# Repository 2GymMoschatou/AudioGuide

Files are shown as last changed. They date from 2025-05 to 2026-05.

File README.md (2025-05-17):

# AudioGuide
Αυτόνομο όχημα ηχητικής ξενάγησης

Πολλές φορές, για την ξενάγηση σε διάφορους χώρους ή μουσεία, μπορεί να είναι χρήσιμη η ηχητική παρουσίαση των εκθεμάτων για άτομα με προβλήματα όρασης. Με τη χρήση ενός ρομπότ-ξεναγού, μπορούμε να βοηθήσουμε τα άτομα αυτά να ξεναγηθούν στο μουσείο.
Το ρομπότ ακολουθεί μια προκαθορισμένη διαδρομή, σχεδιασμένη στο δάπεδο του χώρου των εκθεμάτων και σταματά διαδοχικά μπροστά σε κάθε έκθεμα. Σταματώντας, περιγράφει το έκθεμα και περιμένει την κατάλληλη εντολή για να συνεχίσει στο επόμενο, όπου η λειτουργία επαναλαμβάνεται. Όταν τελειώσει η ξενάγηση στα εκθέματα του χώρου, το ρομπότ επανέρχεται στην αφετηρία της διαδρομής, για να περιμένει την έναρξη ενός νέου κύκλου ξενάγησης.

Υλικά και κόστος του αυτόνομου οχήματος ηχητικής ξενάγησης:

|  Υλικά  |  Κόστος  |
|  ---  |  ---  |
|  Arduino Uno R3 (συμβατό)  |  9,90 €  |
|  Πλατφόρμα κίνησης με 4 κινητήρες  |  16,90 €  |
|  Οδηγός κινητήρων DC L298N  |  5,90 €  |
|  Αισθητήρας υπερύθρων (3 τεμ.)  |  4,80 €  |
|  Αισθητήρας υπερήχων  |  1,80 €  |
|  MP3 player Mini Module	  |  6,80 €  |
|  Κάρτα μνήμης microSDHC 32 Gb	|  6,80 €  |
|  Ηχείο 3W	|	2,40 €  |
|  Push Button|	0,50 €  |
|  Πλακέτα πρωτοτύπου για Arduino  |  1,80 €  |
|  Arduino long headers 6 pin  |  0,50 €  |
|  Arduino long headers 8 pin  |  0,50 €  |
|  Μπαταριοθήκη 6ΑΑ με διακόπτη  |  1,80 €  |
|  Μπαταρίες ΑΑ (6 τεμ.)	|  2,40 €  |
|  Σύνολο  |  62,80 €  |

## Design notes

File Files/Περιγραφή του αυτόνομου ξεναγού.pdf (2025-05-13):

# Αυτόνομο όχημα ηχητικής ξενάγησης

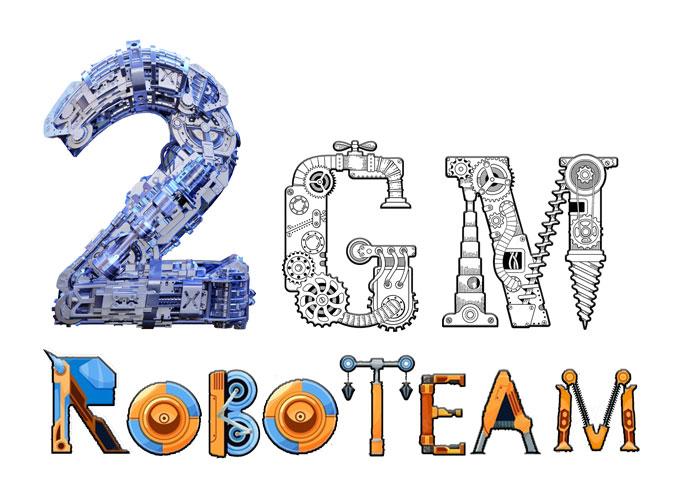
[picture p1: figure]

# 2ο Γυμνάσιο Μοσχάτου

# Σχολικό έτος 2024 - 25

## Περιγραφή του αυτόνομου οχήματος ηχητικής ξενάγησης

Το όχημα του αυτόνομου ξεναγού που σχεδιάσαμε έχει τη δυνατότητα να ακολουθεί μια μαύρη γραμμή στο δάπεδο του χώρου όπου θα κινηθεί. Για να σταματά στα σημεία που επιθυμούμε μπορεί να ανιχνεύσει τις κάθετες μαύρες γραμμές στη διαδρομή. Το όχημα ξεκινά από την είσοδο του χώρου, και ακολουθώντας τη γραμμή, σταματά διαδοχικά στις θέσεις που έχουμε ορίσει. Σε κάθε θέση αναπαράγει το αντίστοιχο αρχείο ήχου που έχουμε αποθηκεύσει στην κάρτα μνήμης. Για να ξεκινήσει από κάθε θέση και να προχωρήσει στην επόμενη, πρέπει να λάβει την κατάλληλη εντολή με το πάτημα ενός μπουτόν. Αν το όχημα ανιχνεύσει κάποιο εμπόδιο στη διαδρομή, τότε σταματά και περιμένει μέχρι να απομακρυνθεί το εμπόδιο.
Το όχημα θα μπορεί να χρησιμοποιηθεί βοηθητικά σε χώρους εκθέσεων, ιδιαίτερα για άτομα με προβλήματα όρασης.

## Σχεδίαση του αυτόνομου οχήματος ηχητικής ξενάγησης

Για την υλοποίηση του οχήματος χρησιμοποιήθηκε μια ρομποτική πλατφόρμα με τέσσερις κινητήρες DC, οι οποίοι ελέγχονται από μια πλακέτα με το ολοκληρωμένο ελέγχου L298N. Η ανίχνευση της διαδρομής του οχήματος πραγματοποιείται με τη βοήθεια τριών αισθητήρων υπερύθρων και η ανίχνευση τυχόν εμποδίων στη διαδρομή με ένα αισθητήρα υπερήχων. Η αναπαραγωγή των αρχείων ήχου γίνεται από μια μονάδα MP3 Player στην οποία συνδέεται ένα ηχείο 3 Watt. Η μονάδα διαθέτει μια υποδοχή για κάρτα μνήμης SD, όπου είναι αποθηκευμένα τα αρχεία ήχου. Οι εντολές για την κίνηση του οχήματος δίνονται από ένα μπουτόν. Το όχημα τροφοδοτείται από μια συστοιχία 6 μπαταριών ΑΑ, η οποίες περιέχονται σε μια μπαταριοθήκη με διακόπτη. Για τον έλεγχο του οχήματος χρησιμοποιείται η πλακέτα Arduino Uno.
Οι συνδέσεις των στοιχείων του οχήματος φαίνονται στο παρακάτω σχήμα:

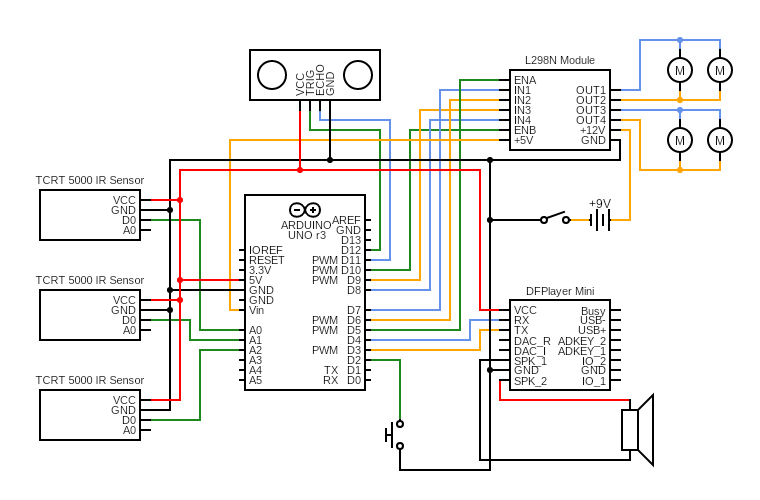
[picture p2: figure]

Το διάγραμμα των συνδέσεων δημιουργήθηκε με την δωρεάν online εφαρμογή δημιουργίας διαγραμμάτων ηλεκτρονικών κυκλωμάτων στη διεύθυνση www.circuit-diagram.org

## Συναρμολόγηση του αυτόνομου οχήματος ηχητικής ξενάγησης

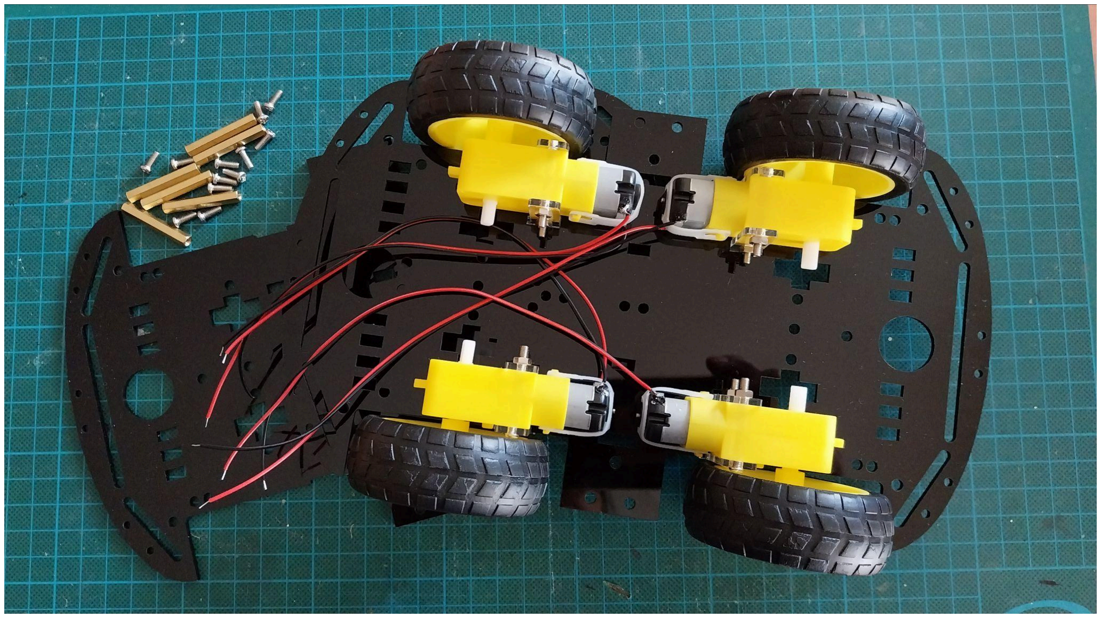
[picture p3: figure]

Η κατασκευή του οχήματος ξεκίνησε με την
τοποθέτηση των κινητήρων στο ένα τμήμα από το
σασί της πλατφόρμας.

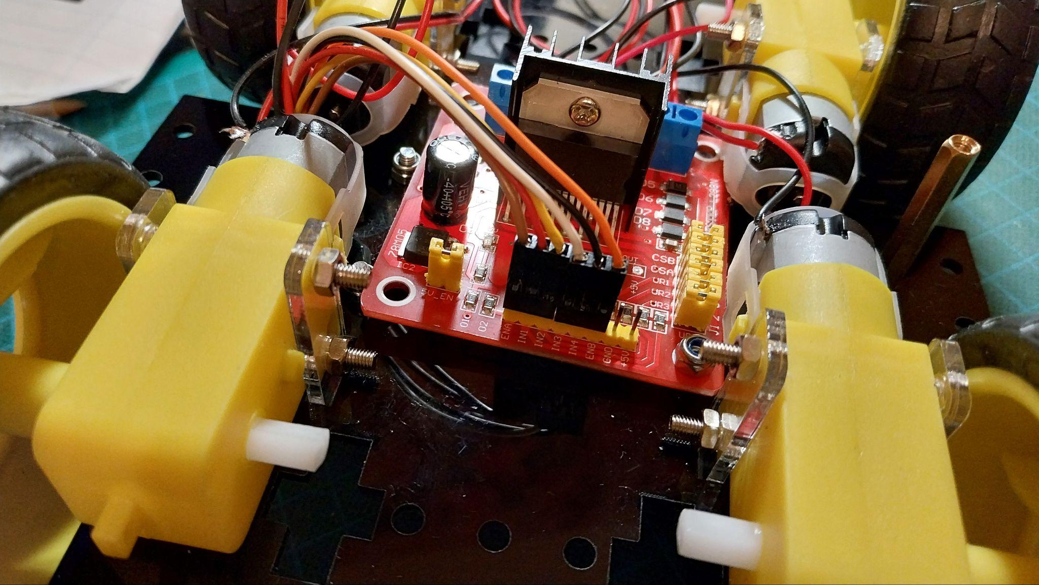
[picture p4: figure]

Ανάμεσα στους κινητήρες τοποθετήθηκε η πλακέτα με το ολοκληρωμένο L298N για την οδήγηση των κινητήρων. Στην πλακέτα συνδέθηκαν οι κινητήρες και η μπαταριοθήκη για την τροφοδοσία του οχήματος. Επίσης προετοιμάστηκαν οι καλωδιώσεις για τη σύνδεση με την πλακέτα του Arduino Uno.

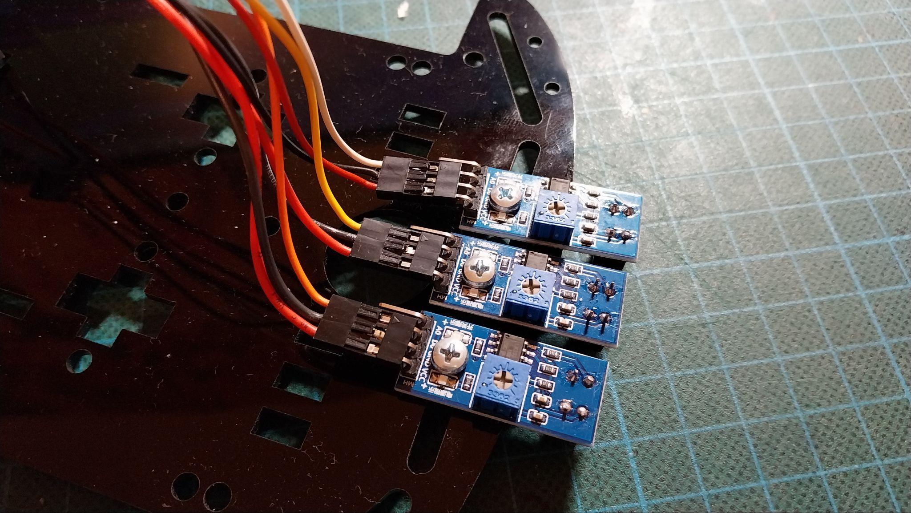
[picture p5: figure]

Στο δεύτερο τμήμα του σασί τοποθετήθηκαν οι αισθητήρες υπερύθρων με τις καλωδιώσεις τους.

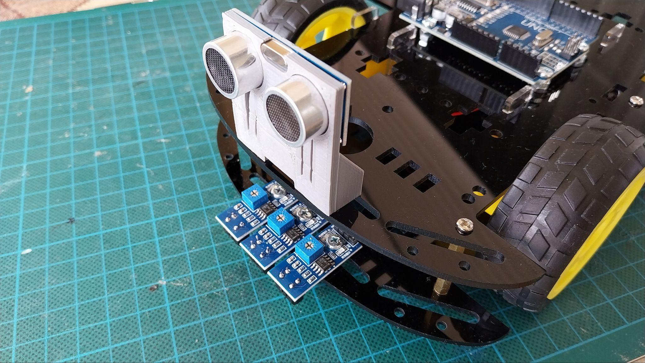
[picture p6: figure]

Τα δύο τμήματα του σασί συνδέθηκαν μεταξύ τους και στο πάνω μέρος του οχήματος τοποθετήθηκε και ο αισθητήρας υπερήχων με τη βάση του.

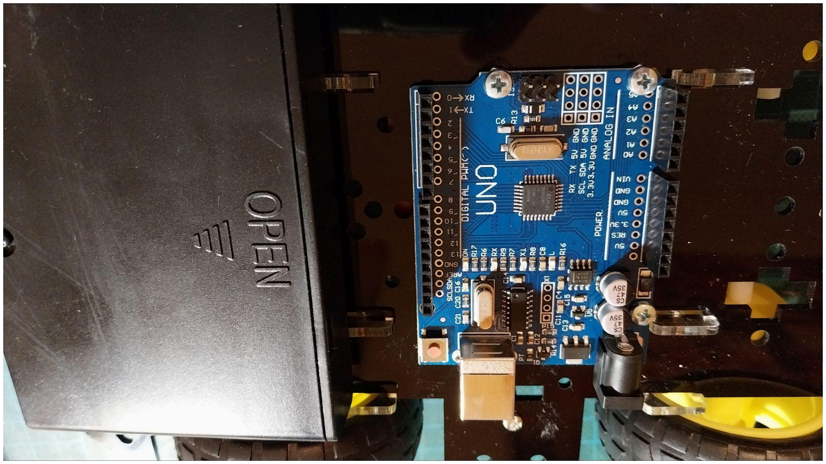
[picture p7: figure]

Στο πάνω τμήμα και στο κέντρο του οχήματος τοποθετήθηκε η πλακέτα του Arduino Uno, ενώ πίσω της τοποθετήθηκε η μπαταριοθήκη για την τροφοδοσία του οχήματος.

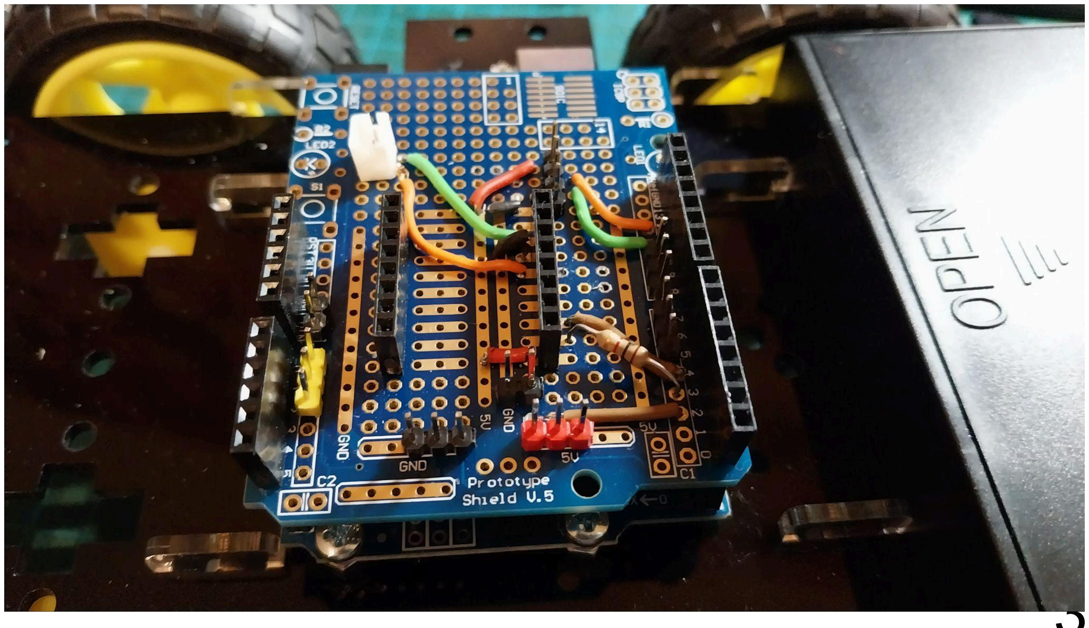
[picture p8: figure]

Στη συνέχεια ετοιμάστηκε η πρωτότυπη πλακέτα με τη βάση για το MP3 Player και τους ακροδέκτες σύνδεσης με τα υπόλοιπα στοιχεία του κυκλώματος και τοποθετήθηκε στο πάνω μέρος της πλακέτας του Arduino Uno.

Η συναρμολόγηση ολοκληρώθηκε με την τοποθέτηση στο μπροστά μέρος του οχήματος της βάσης με το ηχείου και τον διακόπτη εκκίνησης.

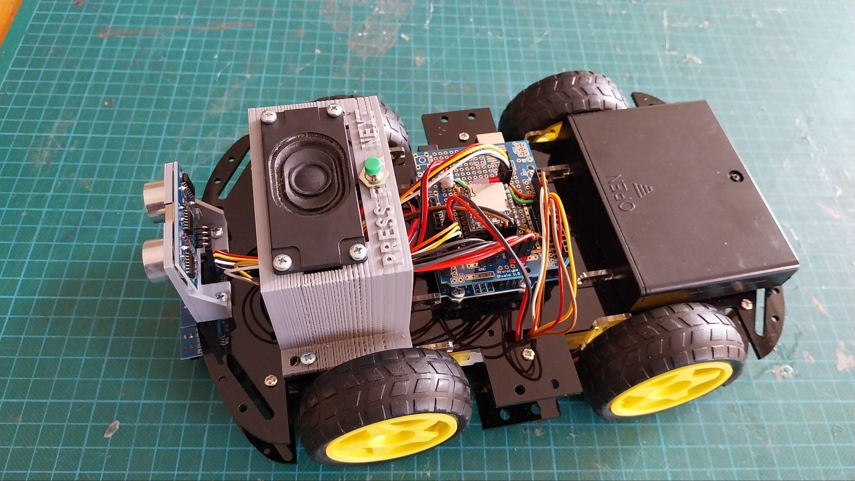
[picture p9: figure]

Τα υλικά που χρησιμοποιούμε στην κατασκευή, καθώς και το κόστος τους φαίνονται στον παρακάτω πίνακα:
Περιγραφή | Τεμάχια | Τιμή μονάδας | Κόστος
Arduino Uno SMD Compatible - CH340 | 1 | 9,90 € | 9,90 €
Ρομποτική πλατφόρμα 4WD - 26 cm | 1 | 16,90 € | 16,90 €
Πλακέτα οδήγησης κινητήρων με το L298 | 1 | 5,90 € | 5,90 €
Αισθητήρας υπερύθρων TCRT5000 | 3 | 1,60 € | 4,80 €
Αισθητήρας υπερήχων HC-SR04 | 1 | 1,80 € | 1,80 €
MP3 Player Mini Module | 1 | 6,80 € | 6,80 €
Κάρτα μνήμης microSDHC 32 GB | 1 | 6,80 € | 6,80 €
Ηχείο 3W 4Ohm | 1 | 2,40 € | 2,40 €
Μπουτόν για στήριξη σε πάνελ | 1 | 0,50 € | 0,50 €
Πλακέτα πρωτοτύπου για Arduino | 1 | 1,80 € | 1,80 €
Arduino Long Headers 6 pin | 2 | 0,25 € | 0,50 €
Arduino Long Headers 8 pin | 2 | 0,25 € | 0,50 €
Μπαταριοθήκη 6 x ΑΑ με διακόπτη | 1 | 1,80 € | 1,80 €
Μπαταρίες ΑΑ | 6 | 0,40 € | 2,40 €
Συνολικό κόστος | | | 62,80 €

Στον παραπάνω πίνακα δεν περιλαμβάνεται το κόστος της καλωδίωσης και των ακροδεκτων για την πλακέτα πρωτοτύπων.

## Κατασκευή μακέτας για την επίδειξη της λειτουργίας

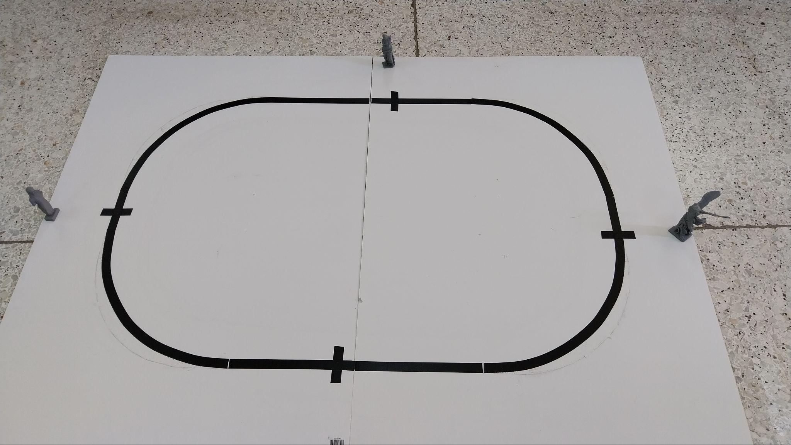
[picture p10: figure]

Για να ελέγξουμε τη λειτουργία του
οχήματος κατασκευάσαμε μια διαδρομή
σχήματος οβάλ πάνω σε χαρτί μακέτας με διαστάσεις 100x140 εκατοστά. Η διαδρομή σημειώθηκε με τη βοήθεια μαύρης μονωτικής ταινίας. Σε τέσσερα σημεία της διαδρομής τοποθετήθηκαν κάθετες γραμμές για τις στάσεις του οχήματος.

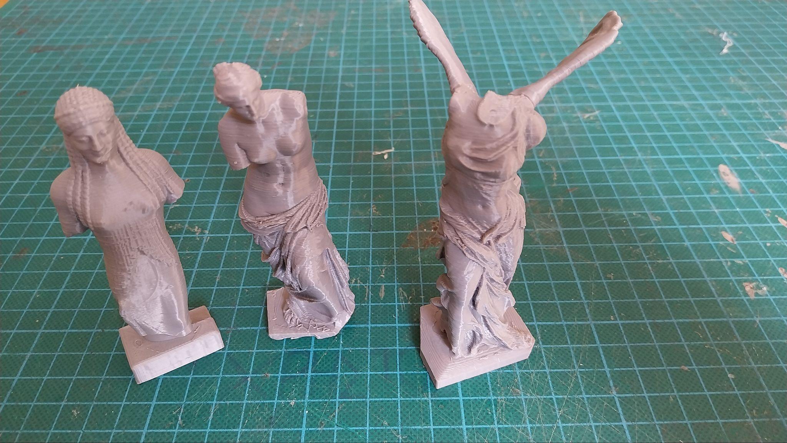
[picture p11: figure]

Για την αναπαράσταση των εκθεμάτων εκτυπώθηκαν τρία αντίγραφα αρχαίων ελληνικών αγαλμάτων. Από τα κείμενα με τις περιγραφές των αγαλμάτων δημιουργήθηκαν, με τη βοήθεια της πλατφόρμας narakeet.com, τα αρχεία mp3 που αναπαράγονται από τη μονάδα του MP3 Player.

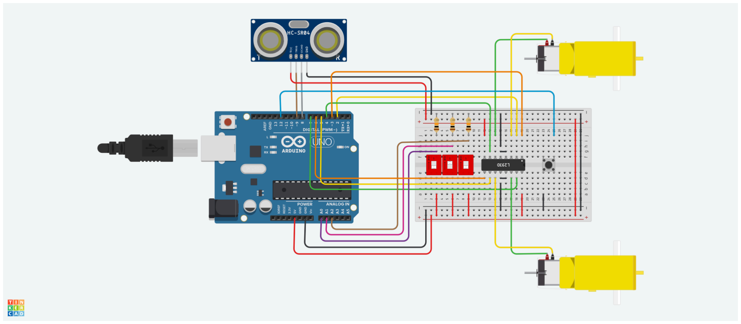
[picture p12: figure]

Για την προσομοίωση της λειτουργίας και του προγραμματισμού των επιμέρους στοιχείων, χρησιμοποιήθηκε το ελεύθερο λογισμικό TinkerCAD. Το ίδιο πρόγραμμα χρησιμοποιήσαμε και για τη σχεδίαση της βάσης του ηχείου και του διακόπτη που κατασκευάσαμε με τον 3D printer.

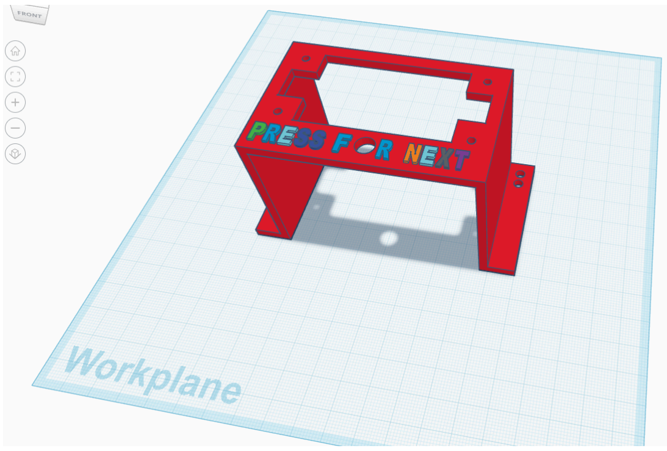
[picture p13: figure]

## Προγραμματισμός του αυτόνομου οχήματος ηχητικής ξενάγησης

Για τον προγραμματισμό του οχήματος χρησιμοποιήθηκε το λογισμικό Arduino IDE.

Στο πρώτο μέρος του προγράμματός εισάγουμε τις απαραίτητες βιβλιοθήκες, δημιουργούμε το αντικείμενο myDFPlayer για τον MP3 Player και ορίζουμε τη σειριακή μέσω software για την επικοινωνία του Arduino με το MP3 Player.

#include <DFRobotDFPlayerMini.h>

#include <SoftwareSerial.h>

SoftwareSerial softSerial(4, 3); //Rx,Tx
DFRobotDFPlayerMini myDFPlayer;

Στη συνέχεια ορίζουμε τους ακροδέκτες του Arduino που θα συνδεθούν με την πλακέτα οδήγησης των κινητήρων.

//Motor A
const int motorPin1 = 7;
const int motorPin2 = 6;
const int enA = 5;
//Motor B
const int motorPin3 = 9;
const int motorPin4 = 8;
const int enB = 10;

Κατόπιν ορίζουμε τους ακροδέκτες, όπου θα συνδεθεί ο αισθητήρας υπερήχων του οχήματος, καθώς και οι μεταβλητές duration, distance και cm τύπου long που θα χρησιμοποιηθούν για τον υπολογισμό της απόστασης από το πλησιέστερο εμπόδιο και θα μεταφέρουν την τιμή στο κυρίως πρόγραμμα.

//Ultrasonic Sensor
const int echoPin = 11;
const int trigPin = 12;
long duration, distance, cm;

Επίσης ορίζουμε τους ακροδέκτες, όπου θα συνδεθούν οι αισθητήρες υπερύθρων και οι μεταβλητές leftID, middleID και rightID για των αποθήκευση των τιμών τους.

//IR sensors
const int leftIR = A2;
const int middleIR = A1;
const int rightIR = A0;
int leftID, middleID, rightID;

Τέλος ορίζουμε τον ακροδέκτη σύνδεσης του διακόπτη εκκίνησης και τη μεταβλητή που αποθηκεύει την τιμή του διακόπτη. Επίσης ορίζουμε τη μεταβλητή moveOn για να αποθηκεύουμε την τιμή 0 ή 1 για τον έλεγχο της κίνησης και τη μεταβλητή track για τον έλεγχο του αρχείου mp3 που θα αναπαράγεται από τη μονάδα του MP3 Player.

//Button
const int buttonPin = 2;
int buttonState = 1;
int moveOn = 1;
int track = 0;

Στην ενότητα setup, πρώτα καθορίζουμε τον τρόπο λειτουργίας των ακροδεκτών του Arduino με τις εντολές pinMode και την ταχύτητα λειτουργίας των κινητήρων με τις εντολές analogWrite.

void setup() {
//Set pins as outputs
pinMode(motorPin1, OUTPUT); pinMode(motorPin2, OUTPUT); pinMode(motorPin3, OUTPUT); pinMode(motorPin4, OUTPUT); pinMode(enA, OUTPUT);
pinMode(enB, OUTPUT);
analogWrite(enA,140);
analogWrite(enB,140);
//Set pins for ultrasonic sensor pinMode(echoPin, INPUT);
pinMode(trigPin, OUTPUT);
//Set pins as inputs for IR sensors pinMode(leftIR, INPUT);
pinMode(middleIR, INPUT);
pinMode(rightIR, INPUT);
//Set pin as inputs for button
pinMode(buttonPin, INPUT_PULLUP);

Στη συνέχεια ενεργοποιούμε τη σειριακή του Arduino για την επικοινωνία με τον υπολογιστή και την σειριακή μέσω software για την επικοινωνία με τη μονάδα του MP3 Player.

// initialize serial communication at 9600 bits per second:
Serial.begin(9600);
softSerial.begin(9600);

Στη συνέχεια ελέγχουμε τη σύνδεση και τη λειτουργία της μονάδα του MP3 Player. Αν η μονάδα δεν λειτουργεί σωστά, η εκτέλεση του προγράμματος σταματά και εμφανίζονται τα κατάλληλα μηνύματα στη σειριακή. Αν η μονάδα λειτουργεί σωστά, τότε, μετά την εμφάνιση των αντίστοιχων μηνυμάτων, ρυθμίζονται και οι παράμετροι λειτουργίας της.

Serial.println();
Serial.println(F("DFRobot DFPlayer Mini Demo"));
Serial.println(F("Initializing DFPlayer ... (May take 3~5 seconds)"));

if (!myDFPlayer.begin(softSerial, /*isACK = */true, /*doReset = */true)) { //Use serial to communicate with mp3.
Serial.println(F("Unable to begin:"));
Serial.println(F("1.Please recheck the connection!")); Serial.println(F("2.Please insert the SD card!")); while(true);
}
Serial.println(F("DFPlayer Mini online."));
myDFPlayer.setTimeOut(500); //Set serial communictaion time out 500ms myDFPlayer.volume(30); //Set volume value (0~30) myDFPlayer.EQ(DFPLAYER_EQ_NORMAL); //Set different EQ myDFPlayer.outputDevice(DFPLAYER_DEVICE_SD); //Set device we use SD as default
}

Στην ενότητα loop διαβάζουμε τη θέση του διακόπτη εκκίνησης και την απόσταση του οχήματος από το πλησιέστερο εμπόδιο. Όταν στο διακόπτη ανιχνεύσουμε χαμηλό δυναμικό, τότε εκτελείται η υπορουτίνα go() και το όχημα κινείται για λίγο ώστε να απομακρυνθεί από την κάθετη γραμμή της διαδρομής. Στη συνέχεια ελέγχει την απόσταση του πλησιέστερου εμποδίου και αν είναι μικρότερη από όσο έχουμε ορίσει το όχημα σταματά, αλλιώς καλεί την υπορουτίνα για την κίνηση του οχήματος. Όσο στον διακόπτη εκκίνησης ανιχνεύουμε υψηλό δυναμικό το όχημα παραμένει ακίνητο.

void loop() {
buttonState = digitalRead(buttonPin);
Serial.println(buttonState);
cm = getDistance();
Serial.print (cm);
Serial.println(" cm");
if (buttonState == LOW){
moveOn = 0;
delay(100);
go();
}
if (moveOn == LOW) {
if (cm <= 15){
stop();
Serial.println("stop at object"); }
else {
move();
}
}
else {
Serial.println("Ready");
delay(100);
}
}

Με την υπορουτίνα move() ελέγχουμε την κίνηση του οχήματος. Με την έναρξη της υπορουτίνας διαβάζουμε τις τιμές των αισθητήρων υπερύθρων και ανάλογα με τις τιμές τους καλούμε τις υπορουτίνες για τις διακριτές κινήσεις της πλατφόρμας. Όταν οι αισθητήρες ανιχνεύσουν κάθετη γραμμή στην διαδρομή, τότε το όχημα σταματά, αλλάζει η κατάσταση κίνησης και αυξάνεται ο αριθμός του αρχείου mp3 που θα αναπαραχθεί. Τέλος καλείται η υπορουτίνα για την αναπαραγωγή του αρχείου mp3. Αν το όχημα βγει εκτός γραμμής τότε κινείται προς τα πίσω μέχρι να ανιχνεύσει ξανά τη γραμμή της διαδρομής στο δάπεδο.

void move(){
leftID = digitalRead(leftIR);
middleID = digitalRead(middleIR);
rightID = digitalRead(rightIR);
if (leftID==HIGH && middleID==HIGH && rightID==HIGH){ stop();
Serial.println("stop");
moveOn = 1;
track = track + 1;
Serial.print("track=");
Serial.println(track);
playSong(); //Play mp3
delay(1000);
}
else if (leftID==LOW && middleID==HIGH && rightID==LOW){ forward();
Serial.println("forward");
}
else if (leftID==HIGH && middleID==HIGH && rightID==LOW){ turnLeft();
Serial.println("turnLeft");
}
else if (leftID==LOW && middleID==HIGH && rightID==HIGH){ turnRight();
Serial.println("turnRight");
}
else if (leftID==HIGH && middleID==LOW && rightID==LOW){ sharpTurnLeft();
Serial.println("sharpTurnLeft");
}
else if (leftID==LOW && middleID==LOW && rightID==HIGH){ sharpTurnRight();
Serial.println("sharpTurnRight");
}
else{
backward();
Serial.println("backward"); }
Serial.print(leftID);

Serial.print(middleID);
Serial.println(rightID);
}

Οι υπορουτίνες forward(), backward(), turnLeft(), turnRight(), sharpTurnLeft(), sharpTurnRight() και stop() εκτελούν τις στοιχειώδεις κινήσεις της πλατφόρμας, ελέγχοντας την φορά περιστροφής κάθε πλευράς κινητήρων. Οι υπορουτίνες αυτές καλούνται από την υπορουτίνα move() που ελέγχει την κίνηση ανάλογα με τις ενδείξεις των αισθητήρων υπερύθρων.

void forward(){
// This code will move the platform forward for 10ms. digitalWrite(motorPin1, HIGH); digitalWrite(motorPin2, LOW); digitalWrite(motorPin3, HIGH); digitalWrite(motorPin4, LOW); delay(10);
}

void backward(){
// This code will move the platform backward for 10ms. digitalWrite(motorPin1, LOW); digitalWrite(motorPin2, HIGH); digitalWrite(motorPin3, LOW); digitalWrite(motorPin4, HIGH); delay(10);
}

void turnLeft(){
//This code will turn the platform left for 10ms. digitalWrite(motorPin1, HIGH); digitalWrite(motorPin2, LOW); digitalWrite(motorPin3, LOW); digitalWrite(motorPin4, LOW); delay(10);
}

void turnRight(){
//This code will turn the platform right for 10ms. digitalWrite(motorPin1, LOW); digitalWrite(motorPin2, LOW); digitalWrite(motorPin3, HIGH); digitalWrite(motorPin4, LOW); delay(10);
}

void sharpTurnLeft(){
//This code will turn the platform sharp left for 10ms.

digitalWrite(motorPin1, HIGH); digitalWrite(motorPin2, LOW); digitalWrite(motorPin3, LOW); digitalWrite(motorPin4, HIGH); delay(10);
}

void sharpTurnRight(){
//This code will turn the platform sharp right for 10ms. digitalWrite(motorPin1, LOW); digitalWrite(motorPin2, HIGH); digitalWrite(motorPin3, HIGH); digitalWrite(motorPin4, LOW); delay(10);
}

void stop(){
//This code will stop the platform. digitalWrite(motorPin1, LOW); digitalWrite(motorPin2, LOW); digitalWrite(motorPin3, LOW);
digitalWrite(motorPin4, LOW);
}

Με την υπορουτίνα getDistance(), υπολογίζουμε την απόσταση του οχήματος από το πλησιέστερο εμπόδιο. Εισάγουμε την υπορουτίνα με τη λέξη long για να δηλώσουμε ότι θα επιστρέψει μια τιμή αυτού του τύπου. Η τιμή επιστρέφεται από την υπορουτίνα, μετά τον υπολογισμό της, με την εντολή return.

long getDistance(){
digitalWrite(trigPin, LOW);
delayMicroseconds(2);
digitalWrite(trigPin, HIGH); delayMicroseconds(10);
digitalWrite(trigPin, LOW); duration = pulseIn(echoPin, HIGH); distance = (duration/2) / 29.1;
return distance;
}

Με την υπορουτίνα go() ξεκινά το όχημα μετά από κάθε στάση. Το όχημα κινείται προς τα μπρος για 200 ms, ώστε να υπερπηδήσει τη κάθετη μαύρη γραμμή στη διαδρομή στην οποία σταμάτησε. Ο χρόνος αυτός εξαρτάται από το πάχος της κάθετης γραμμής που χρησιμοποιούμε.

void go(){
digitalWrite(motorPin1, HIGH);
digitalWrite(motorPin2, LOW);

digitalWrite(motorPin3, HIGH); digitalWrite(motorPin4, LOW);
delay(200);
}

Με την υπορουτίνα playSong() καλούμε το αντικείμενο του MP3 Player και αναπαράγουμε το αρχείο mp3 που μας δείχνει η μεταβλητή track. Όταν η μεταβλητή μας πάρει την μέγιστη τιμή, ανάλογα με τον αριθμό των στάσεων και των αρχείων που αναπαράγουμε, τότε τη μηδενίζουμε για να επαναληφθεί η διαδικασία.

void playSong(){
myDFPlayer.play(track);
if (track == 4){
track = 0;
}
}

## Βιβλιογραφία

1. Βασίλης Νούσης, “ARDUINO για αρχάριους”, 2019 (http://3gym-igoum.thesp.sch.gr/images/Arduino/book.pdf)
2. Εμμανουήλ Πουλάκης, “Προγραμματίζοντας με τον μικροελεγκτή Arduino”, 2015 (https://www.openbook.gr/programmatizontas-me-ton-mikroelegkti-arduino/)
3. Γεώργιος Γίδας, Ευάγγελος Μαντζάνας, “Εφαρμογές Arduino στο σχολικό εργαστήριο για το περιβάλλον”, 2021 (https://www.openbook.gr/efarmoges-arduino-sto-scholiko-ergastirio-gia-to-perivallon/)
4. Νικόλαος Φανουράκης, “Εκπαιδευτική Ρομποτική με τον μικροελεγκτή Arduino”, 2019 (https://www.openbook.gr/ekpaideytiki-rompotiki-me-ton-mikroelegkti-arduino/)

## Ιστοσελίδες

1. https://github.com/DFRobot/DFRobotDFPlayerMini
2. https://wiki.dfrobot.com/DFPlayer_Mini_SKU_DFR0299

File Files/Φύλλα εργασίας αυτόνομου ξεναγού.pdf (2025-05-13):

# Αυτόνομο όχημα ηχητικής ξενάγησης


# Φύλλα εργασίας

# 2ο Γυμνάσιο Μοσχάτου

# Σχολικό έτος 2024 - 25

## Εισαγωγή

Τα φύλλα εργασίας που περιλαμβάνονται στις παρούσες σημειώσεις εξηγούν τη λειτουργία και τη χρήση των επιμέρους στοιχείων που χρησιμοποιούμε στο αυτόνομο όχημα ηχητικής ξενάγησης. Η εκτέλεση των δραστηριοτήτων μπορεί να γίνει εξ ολοκλήρου στο ελεύθερο λογισμικό TinkerCAD και δεν απαιτείται η αγορά εξοπλισμού. Για τη δωρεάν χρήση του TinkerCAD απαιτείται η δημιουργία ενός λογαριασμού μέσω της ιστοσελίδας του προγράμματος.

## Φύλλο εργασίας 1 - Ανάγνωση ψηφιακού αισθητήρα (διακόπτη) και εγγραφή ψηφιακών δεδομένων

Ένας τρόπος εισαγωγής δεδομένων και αλληλεπίδρασης με το Arduino, είναι το πάτημα ενός διακόπτη, το οποίο μπορεί να προκαλεί κάποια άλλη ενέργεια. Οι διακόπτες είναι απλά εξαρτήματα που έχουν μόνο δύο καταστάσεις: ανοιχτός ή κλειστός. Όταν ο διακόπτης είναι κλειστός τότε περνάει ρεύμα από αυτόν, ενώ όταν ο διακόπτης είναι ανοιχτός δεν περνάει ρεύμα. Μερικοί διακόπτες πίεσης κλείνουν όταν τους πιέζουμε, ενώ μερικοί ανοίγουν.
Για την εμφάνιση των δεδομένων μπορεί να χρησιμοποιηθεί το ενσωματωμένο LED στον ακροδέκτη 13 του Arduino ή, εφόσον αυτό δεν επαρκεί, να συνδεθούν εξωτερικά LED σε οποιονδήποτε ψηφιακό ακροδέκτη του.

Α. Ανάγνωση ψηφιακών δεδομένων - σύνδεση pull-down
Σχεδιάζουμε το παρακάτω κύκλωμα στο TINKERCAD:

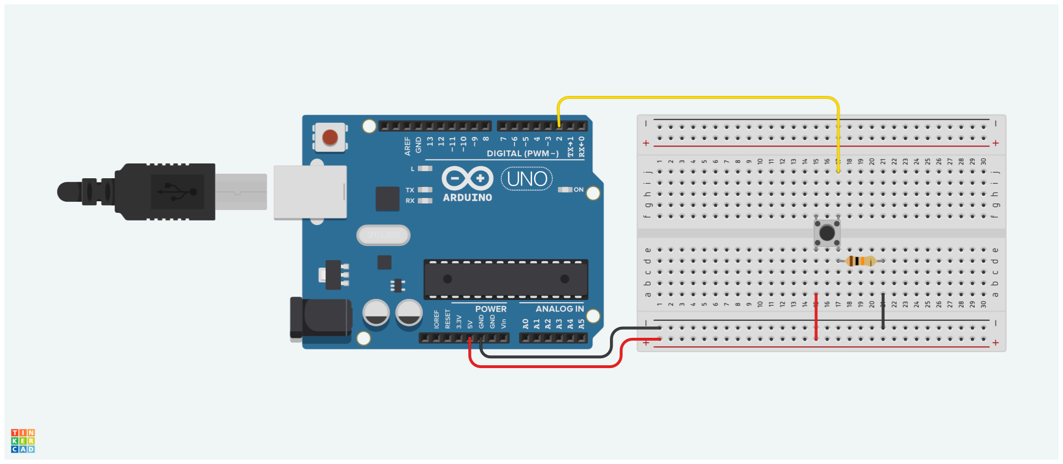
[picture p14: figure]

Η αντίσταση του κυκλώματος έχει τιμή 10KΩ. Με την παραπάνω σύνδεση ο ακροδέκτης 2 του Arduino συνδέεται στη γείωση μέσω της αντίστασης και όταν πατηθεί ο διακόπτης συνδέεται στα 5V.

Εισάγουμε τον παρακάτω κώδικα:
int buttonPin = 2;
int LED = 13;
void setup() {
pinMode(buttonPin, INPUT); pinMode(LED, OUTPUT);
}
void loop() {
int buttonValue = digitalRead(buttonPin); if (buttonValue == HIGH) { digitalWrite(LED,HIGH);
} else {
digitalWrite(LED, LOW);
}
}

Το πρόγραμμα διαβάζει την τιμή του διακόπτη πίεσης και εμφανίζει την κατάστασή του στο ενσωματωμένο LED του Arduino.

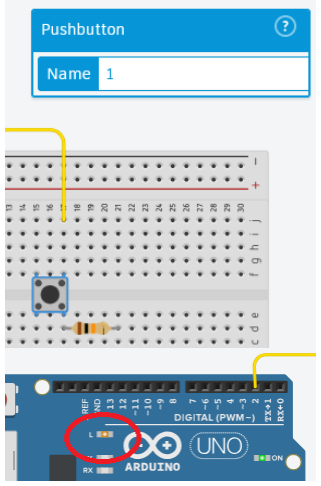
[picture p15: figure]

Ξεκινάμε την προσομοίωση του κυκλώματος στο
TinkerCAD.

Επιλέγουμε τον διακόπτη στον χώρο σχεδίασης και πιέζουμε:

Παρατηρούμε την εναλλαγή στο ενσωματωμένο LED του Arduino. Όταν πιέζεται ο διακόπτης το ενσωματωμένο LED ανάβει.

Β. Ανάγνωση ψηφιακών δεδομένων - σύνδεση pull-up Τροποποιούμε το κύκλωμα στο TINKERCAD όπως παρακάτω:

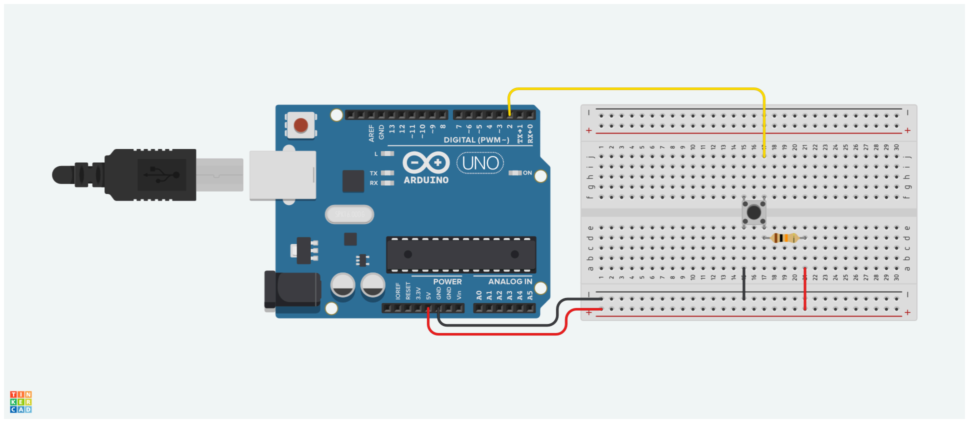
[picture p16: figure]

Με την παραπάνω σύνδεση ο ακροδέκτης 2 του Arduino συνδέεται στα 5V μέσω της αντίστασης και όταν πατηθεί ο διακόπτης συνδέεται στη γείωση.

Δεν κάνουμε καμία τροποποίηση στο πρόγραμμα και ξεκινάμε την προσομοίωση. Το ενσωματωμένο LED είναι αναμμένο και σβήνει όταν πατηθεί ο διακόπτης.

Γ. Ανάγνωση ψηφιακών δεδομένων - ενσωματωμένη αντίσταση pull-up
Η σύνδεση μιας αντίστασης είναι απαραίτητη για τη σωστή λειτουργία ενός διακόπτη. Ωστόσο κάθε ακροδέκτης του Arduino έχει ήδη μια αντίσταση pull-up, που μπορούμε να ενεργοποιήσουμε με μία μόνο αλλαγή στον κώδικα.
Τροποποιούμε το κύκλωμα στο TINKERCAD όπως φαίνεται παρακάτω:

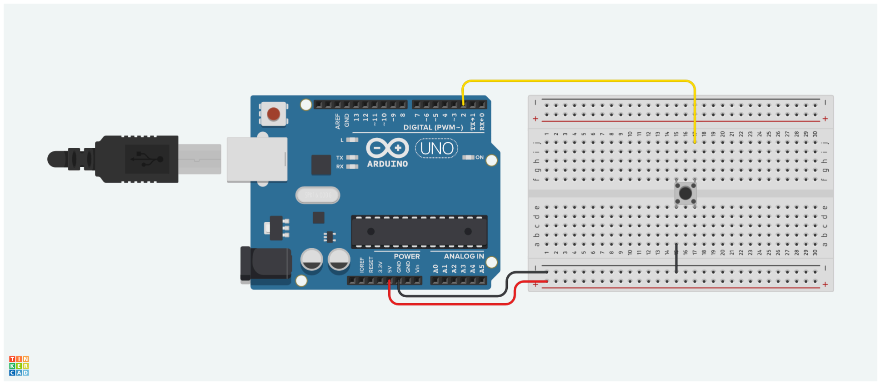
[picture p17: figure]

Τροποποιούμε τον κώδικα, όπως φαίνεται παρακάτω: int buttonPin = 2;
int LED = 13;
void setup() {
pinMode(buttonPin, INPUT_PULLUP); pinMode(LED, OUTPUT);
}
void loop() {
int buttonValue = digitalRead(buttonPin); if (buttonValue == HIGH) { digitalWrite(LED,HIGH);
} else {
digitalWrite(LED, LOW);
}
}

Ξεκινάμε την προσομοίωση του κυκλώματος στο TinkerCAD.
Το κύκλωμα συμπεριφέρεται όπως και στην προηγούμενη περίπτωση.

## Φύλλο εργασίας 2 - Έλεγχος κινητήρων DC με το L293

Ο έλεγχος ενός κινητήρα DC είναι πολύ απλός. Όταν στους ακροδέκτες του κινητήρα εφαρμόζουμε την τάση προς μία κατεύθυνση, ο κινητήρας περιστρέφεται προς τη μία πλευρά, ενώ, αν αντιστρέψουμε την τάση, ο κινητήρας θα γυρίσει αντίθετα. Μπορούμε να ελέγξουμε έναν μικρό κινητήρα συνδέοντάς τον απευθείας με ένα ψηφιακό ακροδέκτη του Arduino. Ωστόσο, κάθε κινητήρας μεγαλύτερος από ένα νόμισμα θα έκαιγε τον ψηφιακό ακροδέκτη και πιθανότατα και το Arduino. Για να οδηγήσουμε έναν μεγαλύτερο κινητήρα, πρέπει να χρησιμοποιήσουμε ένα κύκλωμα με τρανζίστορ ή κάποιο ειδικό ολοκληρωμένο, Με το ολοκληρωμένο οδήγησης L293D, μπορούμε να ελέγξουμε δύο κινητήρες DC.

Α. Έλεγχος της κατεύθυνσης δύο κινητήρων DC με το L293
Σχεδιάζουμε το παρακάτω κύκλωμα στο TINKERCAD:

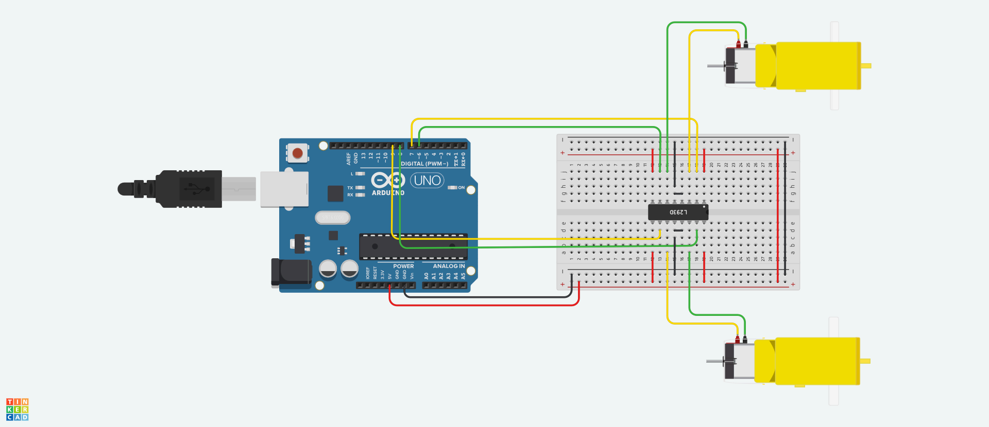
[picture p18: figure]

Εισάγουμε τον παρακάτω κώδικα: //Motor A
const int motorPin1 = 7;
const int motorPin2 = 6;
//Motor B
const int motorPin3 = 9;
const int motorPin4 = 8;

//This will run only one time.
void setup(){
//Set pins for motors
pinMode(motorPin1, OUTPUT); pinMode(motorPin2, OUTPUT); pinMode(motorPin3, OUTPUT); pinMode(motorPin4, OUTPUT);

//This code will turn Motor A clockwise for 2 sec. digitalWrite(motorPin1, HIGH); digitalWrite(motorPin2, LOW); digitalWrite(motorPin3, LOW);

digitalWrite(motorPin4, LOW);
delay(2000);

// This code will turn Motor A & B clockwise for 2 sec. digitalWrite(motorPin1, HIGH); digitalWrite(motorPin2, LOW); digitalWrite(motorPin3, HIGH); digitalWrite(motorPin4, LOW);
delay(2000);

//This code will turn Motor B clockwise for 2 sec. digitalWrite(motorPin1, LOW); digitalWrite(motorPin2, LOW); digitalWrite(motorPin3, HIGH);
digitalWrite(motorPin4, LOW);
delay(2000);

//This code will turn Motor B counter-clockwise for 2 sec. digitalWrite(motorPin1, LOW);
digitalWrite(motorPin2, LOW);
digitalWrite(motorPin3, LOW);
digitalWrite(motorPin4, HIGH);
delay(2000);

//This code will turn Motor A clockwise for 1 sec. digitalWrite(motorPin1, HIGH); digitalWrite(motorPin2, LOW); digitalWrite(motorPin3, LOW); digitalWrite(motorPin4, LOW);
delay(1000);

//This code will turn Motor B clockwise for 1 sec. digitalWrite(motorPin1, LOW); digitalWrite(motorPin2, LOW); digitalWrite(motorPin3, HIGH); digitalWrite(motorPin4, LOW); delay(1000);

//And this code will stop motors digitalWrite(motorPin1, LOW); digitalWrite(motorPin2, LOW); digitalWrite(motorPin3, LOW); digitalWrite(motorPin4, LOW); }

void loop(){

}

Το πρόγραμμα περιστρέφει τον κινητήρα Α ή Β ή και τους δύο μαζί διαδοχικά, είτε κατά τη φορά του ρολογιού είτε αντίστροφα. Επειδή η ενεργοποίηση των κινητήρων γίνεται στην ενότητα setup(), η κάθε περιστροφή γίνεται μόνο μια φορά και στο τέλος οι κινητήρες σταματάνε.

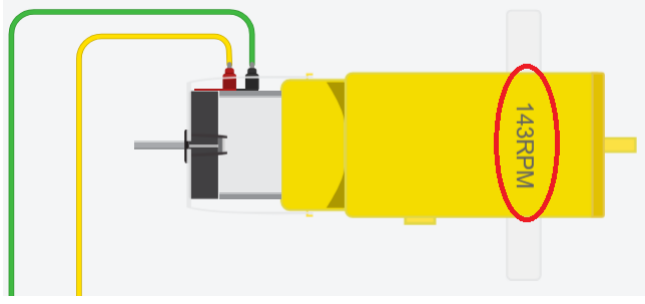
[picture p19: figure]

Ξεκινάμε την προσομοίωση του κυκλώματος στο
TinkerCAD και παρατηρούμε την περιστροφή των
κινητήρων.

Για να επαναληφθεί η ακολουθία των περιστροφών πρέπει να επανεκκινήσουμε την προσομοίωση ή να
πιέσουμε το διακόπτη Reset στο Arduino.
B. Έλεγχος της κατεύθυνσης και της ταχύτητας δύο κινητήρων DC με το L293
Μπορούμε να ελέγξουμε την ταχύτητα ενός κινητήρα χρησιμοποιώντας τη διαμόρφωση πλάτους παλμού (PWM). Χρησιμοποιώντας αυτήν τη μέθοδο, το ρεύμα εφαρμόζεται στον κινητήρα σε σύντομους παλμούς: όσο μεγαλύτερος είναι ο παλμός, τόσο μεγαλύτερη είναι η ταχύτητα,
Τροποποιούμε το κύκλωμα στο TINKERCAD όπως παρακάτω:

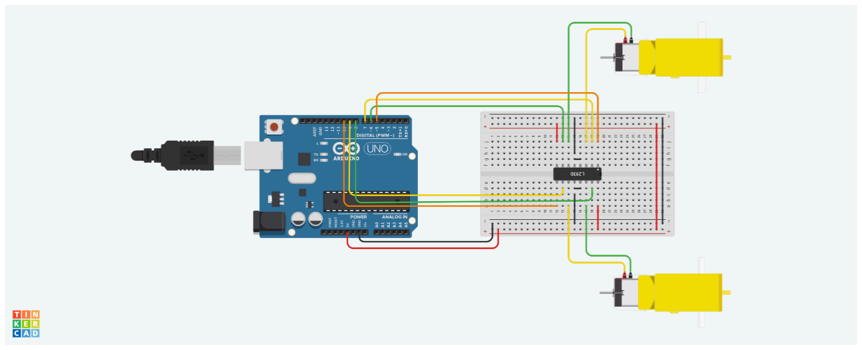
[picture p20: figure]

Εισάγουμε τον παρακάτω κώδικα: //Motor A
const int enA = 5;
const int motorPin1 = 7;
const int motorPin2 = 6;
//Motor B
const int enB = 10;
const int motorPin3 = 9;
const int motorPin4 = 8;

//This will run only one time. void setup(){
//Set pins for motors

pinMode(enA, OUTPUT);
pinMode(enB, OUTPUT);
pinMode(motorPin1, OUTPUT); pinMode(motorPin2, OUTPUT); pinMode(motorPin3, OUTPUT); pinMode(motorPin4, OUTPUT); }

void loop(){
// turn on motors
digitalWrite(motorPin1, HIGH); digitalWrite(motorPin2, LOW); digitalWrite(motorPin3, HIGH); digitalWrite(motorPin4, LOW);
// accelerate from zero to maximum speed for (int i = 0; i < 256; i++){
analogWrite(enA, i);
analogWrite(enB, i);
delay(20);
}
// decelerate from maximum speed to zero for (int i = 255; i >= 0; --i){
analogWrite(enA, i);
analogWrite(enB, i);
delay(20);
}
// now turn off motors
digitalWrite(motorPin1, LOW); digitalWrite(motorPin2, LOW); digitalWrite(motorPin3, LOW); digitalWrite(motorPin4, LOW);
delay(1000);
}

Το πρόγραμμα περιστρέφει και τους δύο κινητήρες ταυτόχρονα με αυξανόμενη ταχύτητα μέχρι το μέγιστο και στη συνέχεια ελαττώνει την ταχύτητα μέχρι το 0, όπου οι κινητήρες απενεργοποιούνται για 1 δευτερόλεπτο, πριν ο κύκλος επαναληφθεί.

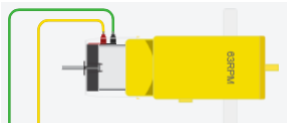
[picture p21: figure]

Ξεκινάμε την προσομοίωση του κυκλώματος στο
TinkerCAD και παρατηρούμε την περιστροφή των
κινητήρων.

## Φύλλο εργασίας 3 - Έλεγχος των κινήσεων μιας ρομποτικής πλατφόρμας με 2 κινητήρες DC και το L293

Μπορούμε να ελέγξουμε την κίνηση μιας ρομποτικής πλατφόρμας ελέγχοντας την κατεύθυνση και την ταχύτητα περιστροφής δύο κινητήρων DC, οι οποίοι είναι τοποθετημένοι στις δύο πλευρές της πλατφόρμας. Αν η πλατφόρμα έχει ερπύστριες, ο κάθε κινητήρας κινεί μια ερπύστρια, ενώ αν η πλατφόρμα έχει τροχούς, ο κάθε κινητήρας ελέγχει έναν τροχό και υπάρχει ένας ή περισσότεροι ελεύθεροι τροχοί για τη στήριξη της πλατφόρμας.

Α. Έλεγχος των κινήσεων μιας ρομποτικής πλατφόρμας
Σχεδιάζουμε το παρακάτω κύκλωμα στο TINKERCAD:

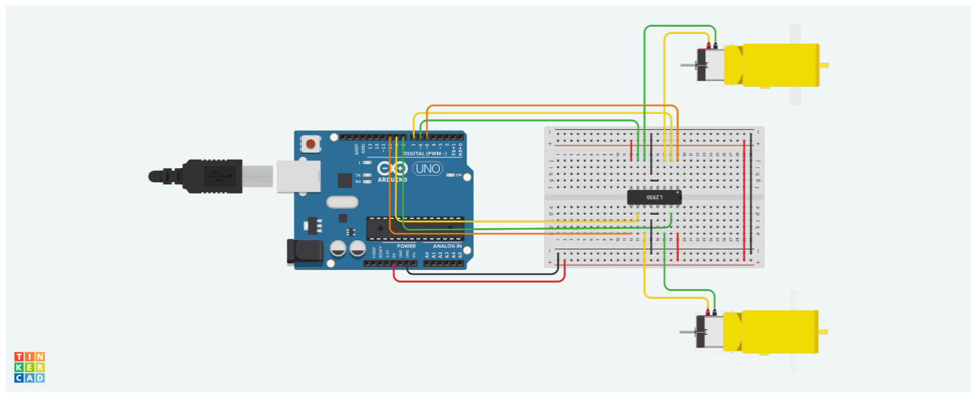
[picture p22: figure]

Εισάγουμε τον παρακάτω κώδικα: //Motor A
const int enA = 5;
const int motorPin1 = 7;
const int motorPin2 = 6;
//Motor B
const int enB = 10;
const int motorPin3 = 9;
const int motorPin4 = 8;

//This will run only one time. void setup(){
//Set pins for motors
pinMode(enA, OUTPUT);
pinMode(enB, OUTPUT);
pinMode(motorPin1, OUTPUT); pinMode(motorPin2, OUTPUT); pinMode(motorPin3, OUTPUT); pinMode(motorPin4, OUTPUT); analogWrite(enA,180);
analogWrite(enB,180);
}

void loop(){
// This code will move platform forward for 1 sec. digitalWrite(motorPin1, HIGH); digitalWrite(motorPin2, LOW); digitalWrite(motorPin3, HIGH); digitalWrite(motorPin4, LOW);
delay(1000);
// This code will move platform backward for 1 sec. digitalWrite(motorPin1, LOW); digitalWrite(motorPin2, HIGH); digitalWrite(motorPin3, LOW); digitalWrite(motorPin4, HIGH); delay(1000);
//This code will turn platform left for 0.5 sec. digitalWrite(motorPin1, HIGH); digitalWrite(motorPin2, LOW); digitalWrite(motorPin3, LOW); digitalWrite(motorPin4, LOW);
delay(500);
//This code will turn platform right for 0.5 sec. digitalWrite(motorPin1, LOW); digitalWrite(motorPin2, LOW); digitalWrite(motorPin3, HIGH); digitalWrite(motorPin4, LOW);
delay(500);
//This code will sharp turn platform left for 0.5 sec. digitalWrite(motorPin1, HIGH); digitalWrite(motorPin2, LOW); digitalWrite(motorPin3, LOW); digitalWrite(motorPin4, HIGH);
delay(500);
//This code will sharp turn platform right for 0.5 sec. digitalWrite(motorPin1, LOW); digitalWrite(motorPin2, HIGH); digitalWrite(motorPin3, HIGH); digitalWrite(motorPin4, LOW); delay(500);
//This code will stop platform for 2 sec. digitalWrite(motorPin1, LOW); digitalWrite(motorPin2, LOW); digitalWrite(motorPin3, LOW); digitalWrite(motorPin4, LOW);
delay(2000);
}

Το πρόγραμμα περιστρέφει τους δύο κινητήρες με την ταχύτητα που ρυθμίζεται από τις εντολές analogWrite() και φορά περιστροφής που καθορίζεται από την πολικότητα των ακροδεκτών. Με την κάθε τετράδα εντολών digitalWrite() εκτελείται και μια κίνηση της πλατφόρμας, η οποία συνεχίζεται για όσο χρόνο καθορίζεται με την εντολή delay(). Αφού εκτελούνται όλες οι πιθανές κινήσεις, οι κινητήρες απενεργοποιούνται για 2 δευτερόλεπτα, πριν ο κύκλος επαναληφθεί.

Ξεκινάμε την προσομοίωση του κυκλώματος στο TinkerCAD και παρατηρούμε την περιστροφή των κινητήρων.

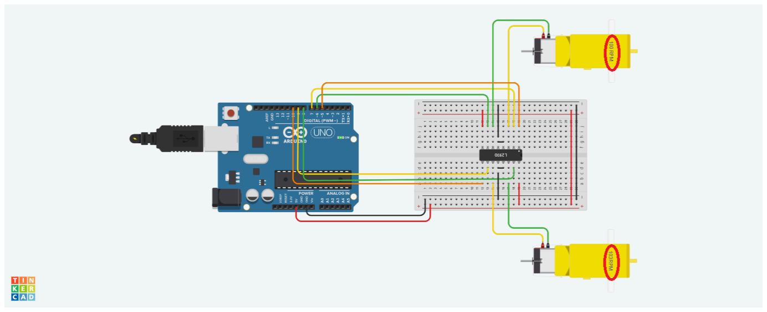
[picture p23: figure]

Β. Έλεγχος των κινήσεων μιας ρομποτικής πλατφόρμας με υπορουτίνες
Χωρίς να μεταβληθεί το κύκλωμα, τροποποιούμε τον κώδικα, δημιουργώντας για κάθε διακριτή κίνηση της πλατφόρμας μια υπορουτίνα και εκτελώντας τες με την ίδια σειρά. Ο κώδικας τροποποιείται ως εξής:
//Motor A
const int enA = 5;
const int motorPin1 = 7;
const int motorPin2 = 6;
//Motor B
const int enB = 10;
const int motorPin3 = 9;
const int motorPin4 = 8;

//This will run only one time. void setup(){
//Set pins for motors
pinMode(enA, OUTPUT);
pinMode(enB, OUTPUT);
pinMode(motorPin1, OUTPUT); pinMode(motorPin2, OUTPUT); pinMode(motorPin3, OUTPUT); pinMode(motorPin4, OUTPUT); analogWrite(enA,180);
analogWrite(enB,180);
}

void loop(){
forward();

backward();
turnLeft();
turnRight();
sharpTurnLeft();
sharpTurnRight();
stop();
}

void forward(){
// This code will move platform forward for 1 sec. digitalWrite(motorPin1, HIGH); digitalWrite(motorPin2, LOW); digitalWrite(motorPin3, HIGH); digitalWrite(motorPin4, LOW); delay(1000);
}

void backward(){
// This code will move platform backward for 1 sec. digitalWrite(motorPin1, LOW); digitalWrite(motorPin2, HIGH); digitalWrite(motorPin3, LOW); digitalWrite(motorPin4, HIGH); delay(1000);
}

void turnLeft(){
//This code will turn platform left for 0.5 sec. digitalWrite(motorPin1, HIGH); digitalWrite(motorPin2, LOW); digitalWrite(motorPin3, LOW); digitalWrite(motorPin4, LOW); delay(500);
}

void turnRight(){
//This code will turn platform right for 0.5 sec. digitalWrite(motorPin1, LOW); digitalWrite(motorPin2, LOW); digitalWrite(motorPin3, HIGH); digitalWrite(motorPin4, LOW); delay(500);
}

void sharpTurnLeft(){
//This code will sharp turn platform left for 0.5 sec. digitalWrite(motorPin1, HIGH); digitalWrite(motorPin2, LOW);

digitalWrite(motorPin3, LOW); digitalWrite(motorPin4, HIGH); delay(500);
}

void sharpTurnRight(){
//This code will sharp turn platform left for 0.5 sec. digitalWrite(motorPin1, LOW); digitalWrite(motorPin2, HIGH); digitalWrite(motorPin3, HIGH); digitalWrite(motorPin4, LOW); delay(500);
}

void stop(){
//This code will stop platform for 2 sec. digitalWrite(motorPin1, LOW); digitalWrite(motorPin2, LOW); digitalWrite(motorPin3, LOW); digitalWrite(motorPin4, LOW);
delay(2000);
}

Όταν ένα τμήμα κώδικα επαναλαμβάνεται αρκετές φορές ή όταν ο κώδικας του κυρίως τμήματος γίνεται πολύπλοκος, μπορούμε να χρησιμοποιήσουμε υπορουτίνες, ώστε ο κώδικας να γίνει πιο εύκολα κατανοητός.
Εισάγουμε τις υπορουτίνες με την παρακάτω μορφή:
void name(){
code
}
Κάθε φορά που θέλουμε να εκτελεστεί ο κώδικας που περιέχεται στην υπορουτίνα, αρκεί να γράψουμε το όνομα της υπορουτίνας:
name();

Ξεκινάμε την προσομοίωση του κυκλώματος στο TinkerCAD. Οι κινητήρες περιστρέφονται με την ίδια φορά και για τον ίδιο χρόνο, όπως και στην προηγούμενη περίπτωση.

## Φύλλο εργασίας 4 - Ακόλουθος γραμμής με αισθητήρες IR και το L293

Ένας συνηθισμένος τρόπος κατεύθυνσης ενός ρομπότ είναι ο ακόλουθος γραμμής, όπου το ρομπότ ακολουθεί μια μαύρη γραμμή σε λευκό πάτωμα με τη βοήθεια αισθητήρων υπερύθρων (IR). Όταν οι υπέρυθρες ανακλώνται στο λευκό πάτωμα ο αισθητήρας δίνει το ψηφιακό 0, ενώ όταν απορροφώνται από τη μαύρη γραμμή δίνει το ψηφιακό 1. Δυστυχώς στο TinkerCAD δεν περιλαμβάνονται αισθητήρες υπερύθρων, οπότε για την προσομοίωση θα χρησιμοποιήσουμε ένα διακόπτη για κάθε αισθητήρα.

Έλεγχος των κινήσεων μιας ρομποτικής πλατφόρμας που ακολουθεί γραμμή Σχεδιάζουμε το παρακάτω κύκλωμα στο TINKERCAD:

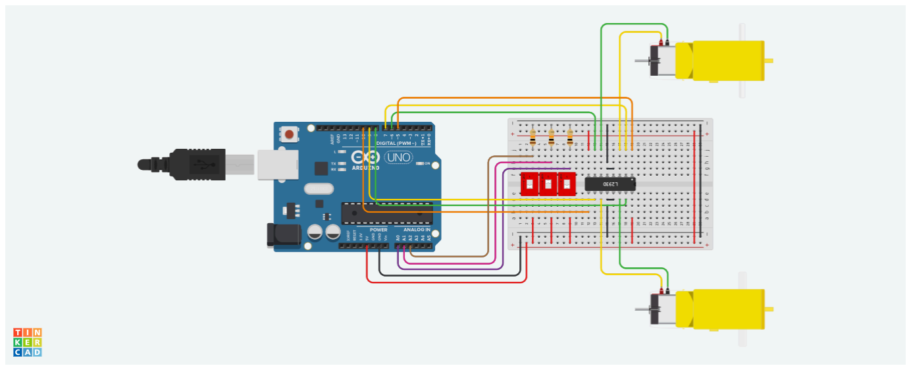
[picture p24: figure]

Για την εξομοίωση των αισθητήρων υπερύθρων χρησιμοποιούμε διακόπτες DIP με αντιστάσεις των 10KΩ σε σύνδεση pull-down.

Εισάγουμε τον παρακάτω κώδικα:
//Motor A
const int enA = 5;
const int motorPin1 = 7;
const int motorPin2 = 6;
//Motor B
const int enB = 10;
const int motorPin3 = 9;
const int motorPin4 = 8;
//IRsensors
const int leftIR = A2;
const int middleIR = A1;
const int rightIR = A0;
int leftID, middleID, rightID;

void setup(){
//Set pins for motors
pinMode(motorPin1, OUTPUT); pinMode(motorPin2, OUTPUT);

pinMode(motorPin3, OUTPUT); pinMode(motorPin4, OUTPUT); pinMode(enA, OUTPUT);
pinMode(enB, OUTPUT);
analogWrite(enA,180);
analogWrite(enB,180);
//Set pins as inputs for IR sensors pinMode(leftIR, INPUT);
pinMode(middleIR, INPUT);
pinMode(rightIR, INPUT);
// initialize serial communication at 9600 bits per second: Serial.begin(9600);
}

void loop(){
leftID = digitalRead(leftIR);
middleID = digitalRead(middleIR);
rightID = digitalRead(rightIR);
if (leftID==HIGH && middleID==HIGH && rightID==HIGH){ stop();
Serial.println("stop");
}
else if (leftID==LOW && middleID==HIGH && rightID==LOW){ forward();
Serial.println("forward");
}
else if (leftID==HIGH && middleID==HIGH && rightID==LOW){ turnLeft();
Serial.println("turnLeft");
}
else if (leftID==LOW && middleID==HIGH && rightID==HIGH){ turnRight();
Serial.println("turnRight");
}
else if (leftID==HIGH && middleID==LOW && rightID==LOW){ sharpTurnLeft();
Serial.println("sharpTurnLeft");
}
else if (leftID==LOW && middleID==LOW && rightID==HIGH){ sharpTurnRight();
Serial.println("sharpTurnRight");
}
else //(leftID==LOW && middleID==LOW && rightID==LOW){ backward();
Serial.println("backward");
}
Serial.print(leftID);
Serial.print(middleID);

S

e

rial.p

rin

tln

(

rig

h

tID

); }void forward(){ // This code will move

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
d. digitalWrite(motorPin1, HIGH); digitalWrite(motorPin2, LOW); digitalWrite(motorPin3, HIGH); digitalWrite(motorPin4, LOW); }void backward(){ // This code will move platform backwar
d. digitalWrite(motorPin1, LOW); digitalWrite(motorPin2, HIGH); digitalWrite(motorPin3, LOW); digitalWrite(motorPin4, HIGH); }void turnLeft(){ //This code will turn platform left. digitalWrite(motorPin1, HIGH); digitalWrite(motorPin2, LOW); digitalWrite(motorPin3, LOW); digitalWrite(motorPin4, LOW); }void turnRight(){ //This code will turn platform right. digitalWrite(motorPin1, LOW); digitalWrite(motorPin2, LOW); digitalWrite(motorPin3, HIGH); digitalWrite(motorPin4, LOW); }void sharpTurnLeft(){ //This code will sharp turn platform left. digitalWrite(motorPin1, HIGH); digitalWrite(motorPin2, LOW); digitalWrite(motorPin3, LOW); digitalWrite(motorPin4, HIGH); }void sharpTurnRight(){ //This code will sharp turn platform left. digitalWrite(motorPin1, LOW); digitalWrite(motorPin2, HIGH); digitalWrite(motorPin3, HIGH); | 1

digitalWrite(motorPin4, LOW); }

void stop(){
//This code will stop platform. digitalWrite(motorPin1, LOW); digitalWrite(motorPin2, LOW); digitalWrite(motorPin3, LOW);
digitalWrite(motorPin4, LOW);
}

Το πρόγραμμα διαβάζει τις τιμές των τριών αισθητήρων υπερύθρων και ανάλογα με τις ενδείξεις καλεί τις υπορουτίνες για τις αντίστοιχες κινήσεις. Αν η πλατφόρμα συναντήσει μια κάθετη μαύρη γραμμή, τότε και οι τρεις αισθητήρες έχουν την τιμή HIGH και η πλατφόρμα σταματά. Αν η πλατφόρμα βγει εκτός της μαύρης γραμμής, τότε και οι τρεις αισθητήρες έχουν την τιμή LOW και η πλατφόρμα οπισθοχωρεί μέχρι να συναντήσει ξανά την γραμμή. Για τον έλεγχο της λειτουργίας του προγράμματος χρησιμοποιούνται οι εντολές Serial.print() και Serial.println(), οι οποίες εμφανίζουν στη σειριακή τις τιμές των αισθητήρων και την κίνηση που αντιστοιχεί.


Ξεκινάμε την προσομοίωση του κυκλώματος στο TinkerCAD
και παρατηρούμε τις ενδείξεις της σειριακής και την
περιστροφή των κινητήρων.


## Φύλλο εργασίας 5 - Μελέτη αισθητήρα υπερήχων

Ο αισθητήρας υπερήχων χρησιμοποιεί ήχο πάνω από την μέγιστη συχνότητα ακοής για να ανιχνεύσει απόσταση. Ο αισθητήρας εκπέμπει ένα σύντομο παλμό ήχου και περιμένει να επιστρέψει. Μετρά τον χρόνο που χρειάζεται για να ταξιδέψει ο ήχος, να ανακλαστεί σε ένα αντικείμενο και μετά να επιστρέψει στον αισθητήρα. Επειδή η ταχύτητα του ήχου είναι γνωστή, ο συνολικός χρόνος που απαιτείται για την επιστροφή του ήχου εξαρτάται από την απόσταση του αντικειμένου.

Α. Μέτρηση απόστασης με τον αισθητήρα υπερήχων
Σχεδιάζουμε το παρακάτω κύκλωμα στο TINKERCAD:


Εισάγουμε τον παρακάτω κώδικα: const int echoPin=11;
const int trigPin=12;
long duration;
long distance;

void setup() {
Serial.begin(9600);
pinMode(trigPin, OUTPUT);
pinMode(echoPin, INPUT);
}

void loop() {
digitalWrite(trigPin, LOW); delayMicroseconds(2);
digitalWrite(trigPin, HIGH); delayMicroseconds(10);
digitalWrite(trigPin, LOW); duration = pulseIn(echoPin, HIGH); distance = (duration/2) / 29.1;

Serial.print(distance);

Serial.println(" cm");
delay(1000);
}

Το πρόγραμμα διαβάζει την απόσταση ενός εμποδίου από τον αισθητήρα υπερήχων και καταγράφει την ένδειξη σε εκατοστά στη σειριακή.

Ξεκινάμε την προσομοίωση του κυκλώματος στο TinkerCAD.


Επιλέγουμε τον αισθητήρα υπερήχων στον χώρο σχεδίασης και μεταβάλλουμε τη θέση του αντικειμένου:

Παρατηρούμε την ένδειξη στη σειριακή:

Β. Χρήση υπορουτίνας για την μέτρηση της απόστασης
Χωρίς να μεταβάλουμε το κύκλωμα, τροποποιούμε τον κώδικα ως εξής: const int echoPin=11;
const int trigPin=12;
long duration;
long distance;
long cm;

void setup() {
Serial.begin(9600);
pinMode(trigPin, OUTPUT);
pinMode(echoPin, INPUT);
}

void loop() {
cm = getDistance();

Serial.print(cm);
Serial.println(" cm");

delay(1000);
}

long getDistance(){
digitalWrite(trigPin, LOW); delayMicroseconds(2);
digitalWrite(trigPin, HIGH); delayMicroseconds(10);
digitalWrite(trigPin, LOW); duration = pulseIn(echoPin, HIGH); distance = (duration/2) / 29.1;
return distance;
}

Μπορούμε να χρησιμοποιήσουμε τις υπορουτίνες για να υπολογίσουμε κάποια μεγέθη και να επιστρέψουμε μόνο τις απαραίτητες τιμές στο κυρίως πρόγραμμα.
Εισάγουμε την υπορουτίνα:
long getDistance(){

}
Η λέξη long στην αρχή σημαίνει ότι η υπορουτίνα θα επιστρέφει στο κυρίως πρόγραμμα μια τιμή τύπου long. Στο εσωτερικό της υπορουτίνας εισάγουμε τις εντολές για την ανάγνωση του αισθητήρα υπερήχων και τον υπολογισμό της απόστασης. Στο τέλος της υπορουτίνας επιστρέφουμε τη μεταβλητή distance στο κυρίως πρόγραμμα με την εντολή:
return distance;
Στην ενότητα setup() εισάγουμε και τη μεταβλητή cm για την αποθήκευση της τιμής που επιστρέφει η υπορουτίνα στο κυρίως πρόγραμμα.
Επαναλαμβάνουμε την προσομοίωση του κυκλώματος στο TinkerCAD, όπου τα αποτελέσματα πρέπει να είναι παρόμοια με την προηγούμενη υλοποίηση.

## Φύλλο εργασίας 6 - Ακόλουθος γραμμής με αποφυγή σύγκρουσης

Ενσωματώνουμε τον αισθητήρα υπερήχων στον ακόλουθο γραμμής και το ρομπότ εκτός από το να ακολουθεί μια μαύρη γραμμή σε λευκό πάτωμα μπορεί να αποφεύγει και τις συγκρούσεις με αντικείμενα που μπορεί να βρεθούν στη διαδρομή του.

Έλεγχος των κινήσεων μιας ρομποτικής πλατφόρμας που ακολουθεί γραμμή και αποφεύγει τα εμπόδια
Σχεδιάζουμε το παρακάτω κύκλωμα στο TINKERCAD:


Εισάγουμε τον παρακάτω κώδικα: //Motor A
const int enA = 5;
const int motorPin1 = 7;
const int motorPin2 = 6;
//Motor B
const int enB = 10;
const int motorPin3 = 9;
const int motorPin4 = 8;
//Ultrasonic Sensor
const int echoPin = 11;
const int trigPin = 12;
long duration, distance, cm; //IRsensors
const int leftIR = A2;
const int middleIR = A1;
const int rightIR = A0;
int leftID, middleID, rightID;

void setup(){
//Set pins for motors
pinMode(motorPin1, OUTPUT);

pinMode(motorPin2, OUTPUT); pinMode(motorPin3, OUTPUT); pinMode(motorPin4, OUTPUT); pinMode(enA, OUTPUT);
pinMode(enB, OUTPUT);
analogWrite(enA,180);
analogWrite(enB,180);
//Set pins for ultrasonic sensor pinMode(echoPin, INPUT);
pinMode(trigPin, OUTPUT);
//Set pins as inputs for IR sensors pinMode(leftIR, INPUT);
pinMode(middleIR, INPUT);
pinMode(rightIR, INPUT);
// initialize serial communication at 9600 bits per second: Serial.begin(9600);
}

void loop(){
cm = getDistance();
Serial.print (cm);
Serial.println(" cm");
if (cm <= 15){
stop();
Serial.println("stop at object"); }
else {
move();
}
}

void move(){
leftID = digitalRead(leftIR);
middleID = digitalRead(middleIR);
rightID = digitalRead(rightIR);
if (leftID==HIGH && middleID==HIGH && rightID==HIGH){ stop();
Serial.println("stop");
}
else if (leftID==LOW && middleID==HIGH && rightID==LOW){ forward();
Serial.println("forward");
}
else if (leftID==HIGH && middleID==HIGH && rightID==LOW){ turnLeft();
Serial.println("turnLeft");
}
else if (leftID==LOW && middleID==HIGH && rightID==HIGH){

turnRight();
Serial.println("turnRight");
}
else if (leftID==HIGH && middleID==LOW && rightID==LOW){ sharpTurnLeft();
Serial.println("sharpTurnLeft");
}
else if (leftID==LOW && middleID==LOW && rightID==HIGH){ sharpTurnRight();
Serial.println("sharpTurnRight");
}
else //(leftID==LOW && middleID==LOW && rightID==LOW){ backward();
Serial.println("backward");
}
Serial.print(leftID);
Serial.print(middleID);
Serial.println(rightID);
}

void forward(){
// This code will move platform forward for 1 sec. digitalWrite(motorPin1, HIGH); digitalWrite(motorPin2, LOW); digitalWrite(motorPin3, HIGH); digitalWrite(motorPin4, LOW);
}

void backward(){
// This code will move platform backward for 1 sec. digitalWrite(motorPin1, LOW); digitalWrite(motorPin2, HIGH); digitalWrite(motorPin3, LOW); digitalWrite(motorPin4, HIGH);
}

void turnLeft(){
//This code will turn platform left for 0.5 sec. digitalWrite(motorPin1, HIGH); digitalWrite(motorPin2, LOW); digitalWrite(motorPin3, LOW); digitalWrite(motorPin4, LOW);
}

void turnRight(){
//This code will turn platform right for 0.5 sec. digitalWrite(motorPin1, LOW); digitalWrite(motorPin2, LOW);

digitalWrite(motorPin3, HIGH); digitalWrite(motorPin4, LOW);
}

void sharpTurnLeft(){
//This code will sharp turn platform left for 0.5 sec. digitalWrite(motorPin1, HIGH); digitalWrite(motorPin2, LOW); digitalWrite(motorPin3, LOW); digitalWrite(motorPin4, HIGH);
}

void sharpTurnRight(){
//This code will sharp turn platform left for 0.5 sec. digitalWrite(motorPin1, LOW); digitalWrite(motorPin2, HIGH); digitalWrite(motorPin3, HIGH); digitalWrite(motorPin4, LOW);
}

void stop(){
//This code will stop platform for 2 sec. digitalWrite(motorPin1, LOW); digitalWrite(motorPin2, LOW); digitalWrite(motorPin3, LOW); digitalWrite(motorPin4, LOW); }

long getDistance(){
digitalWrite(trigPin, LOW); delayMicroseconds(2);
digitalWrite(trigPin, HIGH); delayMicroseconds(10);
digitalWrite(trigPin, LOW); duration = pulseIn(echoPin, HIGH); distance = (duration/2) / 29.1;
return distance;
}

Το πρόγραμμα ελέγχει την απόσταση που έχει διαθέσιμη για να κινηθεί και αν είναι μεγαλύτερη από την καθορισμένη τιμή τότε καλεί την υπορουτίνα της κίνησης για να παρακολουθήσει τη γραμμή στο πάτωμα.

Ξεκινάμε την προσομοίωση του κυκλώματος στο TinkerCAD και παρατηρούμε τη λειτουργία του κυκλώματος μεταβάλλοντας τις τιμές των αισθητήρων καθώς και τις ενδείξεις της σειριακής.
Ένα στιγμιότυπο της προσομοίωσης φαίνεται παρακάτω:


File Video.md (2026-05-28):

Το βίντεο με την παρουσίαση του αυτόνομου ξεναγού βρίσκεται στο κανάλι της ομάδας 2GM_Roboteam στο Youtube: https://youtu.be/pQGIX01Bj5g

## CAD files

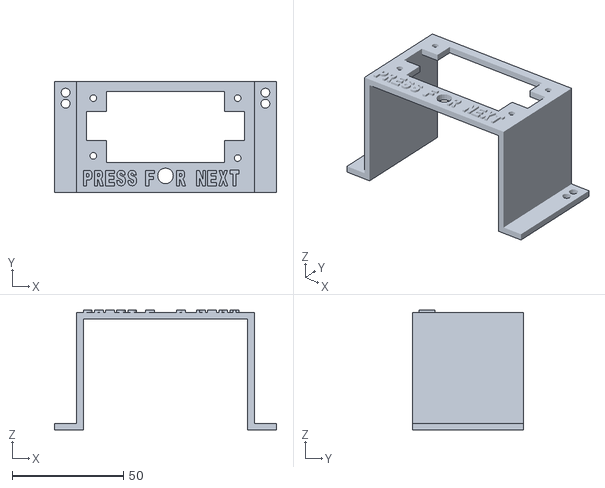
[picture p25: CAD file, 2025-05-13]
Stl/Speaker_base.stl
100.0 x 50.0 x 54.0
